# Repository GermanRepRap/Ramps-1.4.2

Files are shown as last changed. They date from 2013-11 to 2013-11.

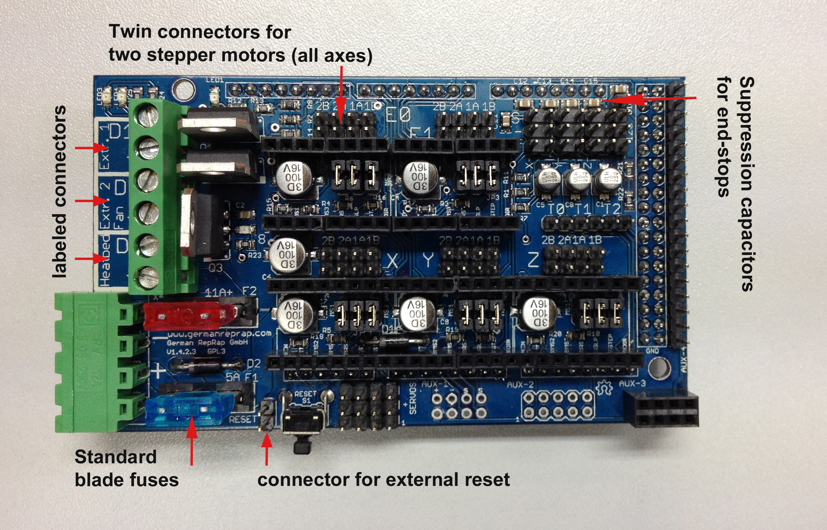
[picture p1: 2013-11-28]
Ramps142_1_beschriftet_EN.jpg

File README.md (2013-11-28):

Ramps-1.4.2
===========

forked from ultimachine/Ramps 1.4

The RAMPS 1.4.2 Change log

* Standard blade fuses instead of thermal fuses increasing the heat resilience.
 	
* Current carrying improved by increasing the thickness of the cooper at the PCB from 35 to 70 micro meters.

* Suppression caps added to each end-stop to avoid spurious signals.

* Added an additional connector to XY, E1 and E2 to connect a second stepper motor.

* Connector for external reset added.

* Labeled D8, D9,D10 with Heatbed, Extrude 1, Fan and Extruder 2.

Fully assembled available from German RepRap www.germanreprap.com

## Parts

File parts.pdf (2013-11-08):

StÃ¼ckliste exportiert aus /Users/markus/Documents/Arbeit/grrf/ ramps 1_42_3/RAMPS_1-42.3.sch am 17.07.13 03:23

Qty Value | Device | Package | Parts | Description | MF MPN OC_FARNELL OC_NEWARK
1 | 31-XX | B3F-31XX | S1 | OMRON SWITCH | B3F-
3100 959704 | 36M3582
10 | 3PIN-HEADER | 3PIN-HEADER

SER1,
SER2,
SER3,
SER4,
X+, X-,
Y+, Y-,
Z+, Z-

PIN HEADER

6 | C-EUC0805 | C0805 | C11, C12, C13, C14, C15, C16 | CAPACITOR, European symbol
2 | FUSE_MCCQ-122 | FUSE_MCCQ-122 | F1, F2
4 | LEDCHIP-LED0805 | CHIP-LED0805 | LED1, LED2, LED3, LED4 | LED
1 | M06SIP | 1X06 | JP7 | Header 6
13 | PINHD-1X4 | 1X04

A-OUT,
E0-
MOT,
E0-
MOT1,
E1-
MOT,
E1-
MOT1,
I2C,
SERIAL,
X-MOT,
X-MOT1,
Y-MOT,
Y-MOT1,
Z-MOT,
Z-MOT1

PIN HEADER

5 | PINHD-2X3 | 2X03

JP2, JP3,
JP4, JP5,
JP6

PIN HEADER

3 | 1.8K | R-US_R0805 | R0805

R23,
R24,
R25

RESISTOR,
American
symbol
8 | 100k | R-US_R0805 | R0805

R2, R3,
R4, R5,
R6, R8,
R9, R10

RESISTOR,
American
symbol
1 | 100nF | C-EUC0805 | C0805 | C2

CAPACITOR,
European
symbol
6 | 100uF | CPOL-US153CLV-0605 | 153CLV-0605 | C3, C4, C6, C7, C9, C10

POLARIZED
CAPACITOR,
American
symbol
5 | 10k | R-US_R0805 | R0805

R16,
R17,
R18,
R19,
R20

RESISTOR,
American
symbol
1 | 10r | R-US_M0805 | M0805 | R14 RESISTOR, American symbol
2 | 10r | R-US_R0805 | R0805 | R13, R15 RESISTOR, American symbol
3 | 10uF | CPOL-US153CLV-0405 | 153CLV-0405 | C1, C5, C8 POLARIZED CAPACITOR, American symbol
1 | 1K | R-US_R0805 | R0805 | R12 RESISTOR, American symbol
2 | 1N4004 | 1N4004 | DO41-10 | D1, D2 DIODE

1 | 282837-6 | 282837-6 | 282837-6 | U$2
5 | 4.7K | R-US_R0805 | R0805

R1, R7,
R11,
R21,
R22

RESISTOR,
American
symbol
5 | A4988BREAKOUT | A4988BREAKOUT | A4988BREAKOUT | U$4,
| | | | U$5,
| | | | U$6,
| | | | U$7,
| | | | U$8
1 | ARDUINO_MEGA_SHIELD ARDUINO_MEGA_SHIELD ARDUINO_MEGA_SHIELD U1
1 | M04X2 | M04X2 | 2X4 | U$3
1 | M05X2 | M05X2 | 2X5 | U$10
1 | M18_ | M18_ | 1X18 | U$9
1 | MSTBA4 | MSTBA4 | MSTBA4 | X4 | PHOENIX
1 | OSHW_LOGO_6MILX0100-
| NT | OSHW_LOGO_6MILX0100-
| | NT | OSHW_6X100_NOTEXT | LOGO1
1 | PINHD-2 | PINHD-2 | PINHD-2 | RESET
3 | STP55NF06L | IRF512 | TO220BV | Q1, Q2,
| | | | Q3 | N-CHANNEL
| | | | | MOS FET

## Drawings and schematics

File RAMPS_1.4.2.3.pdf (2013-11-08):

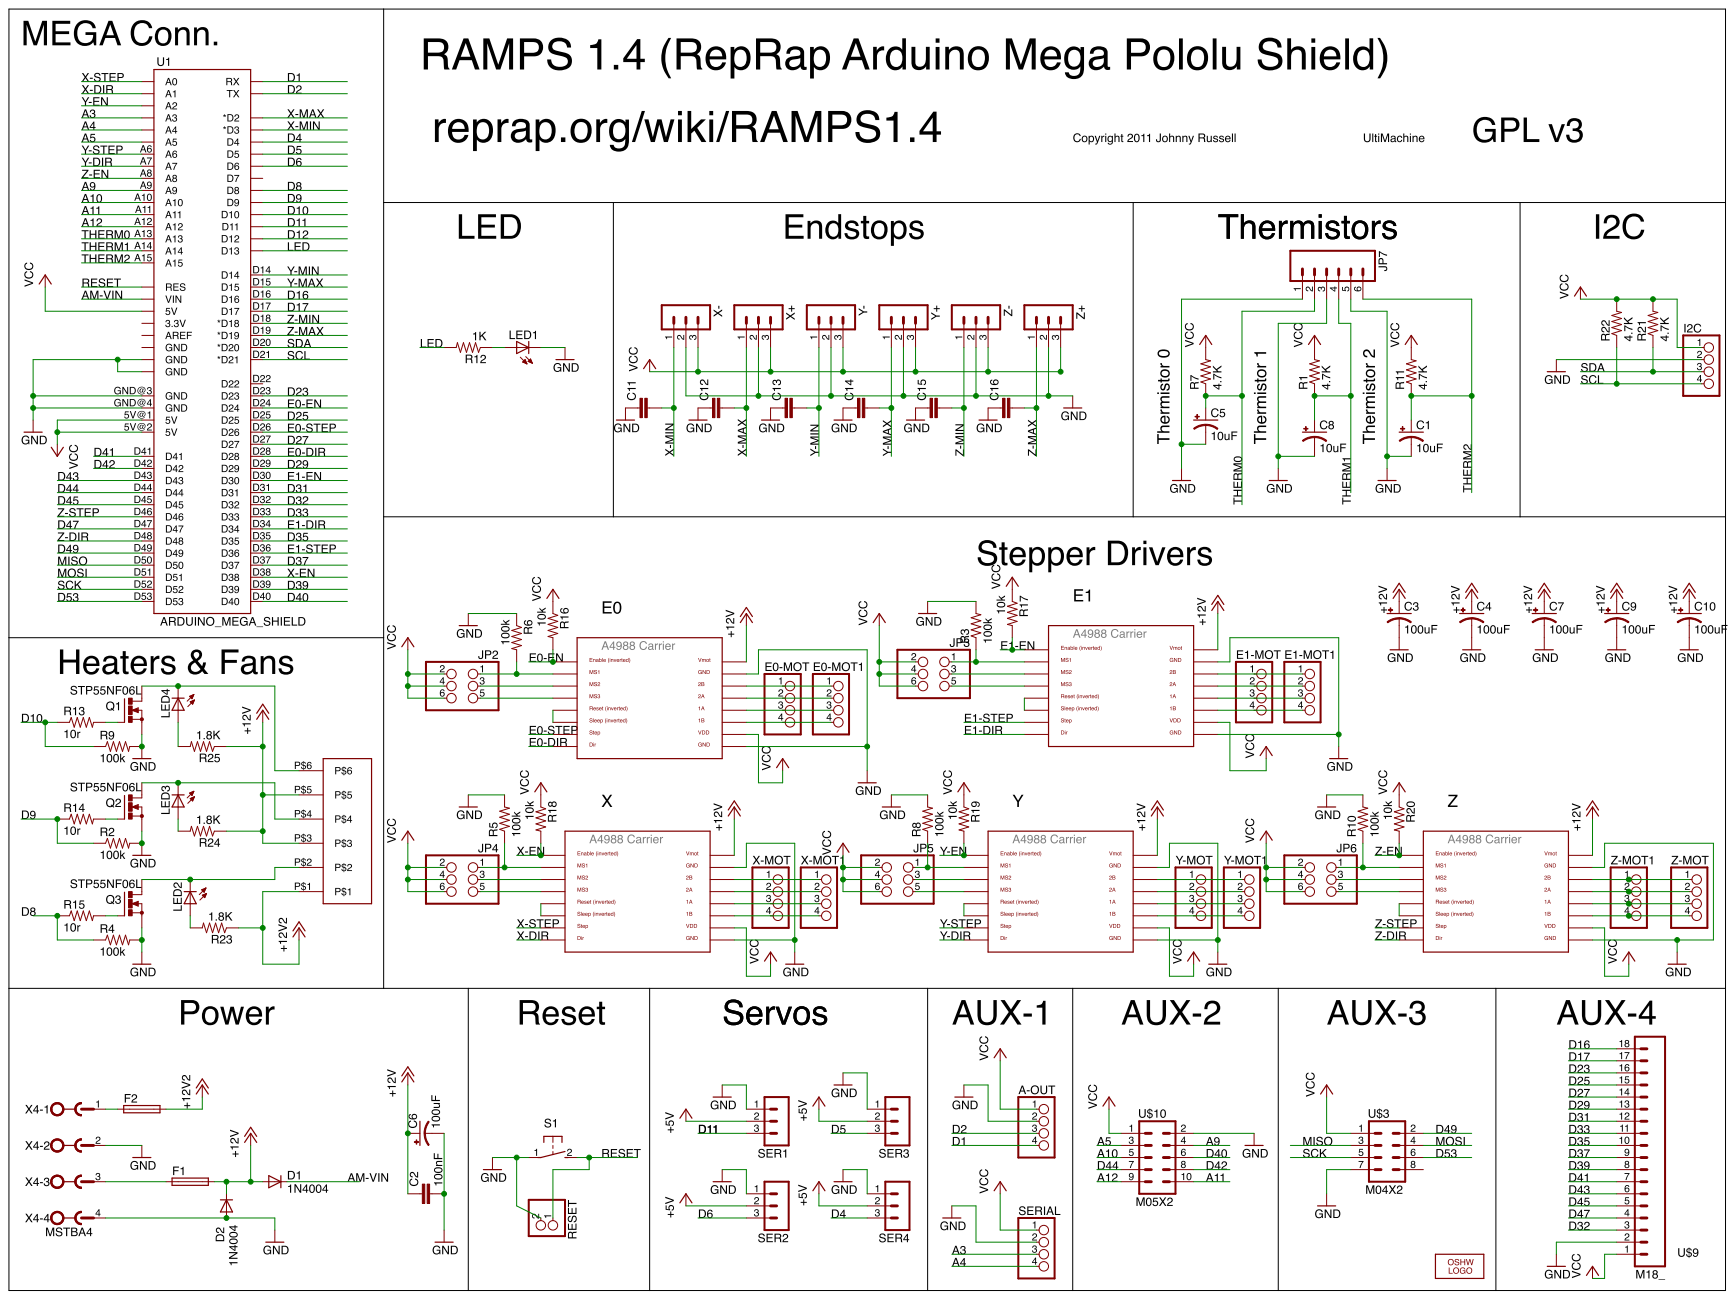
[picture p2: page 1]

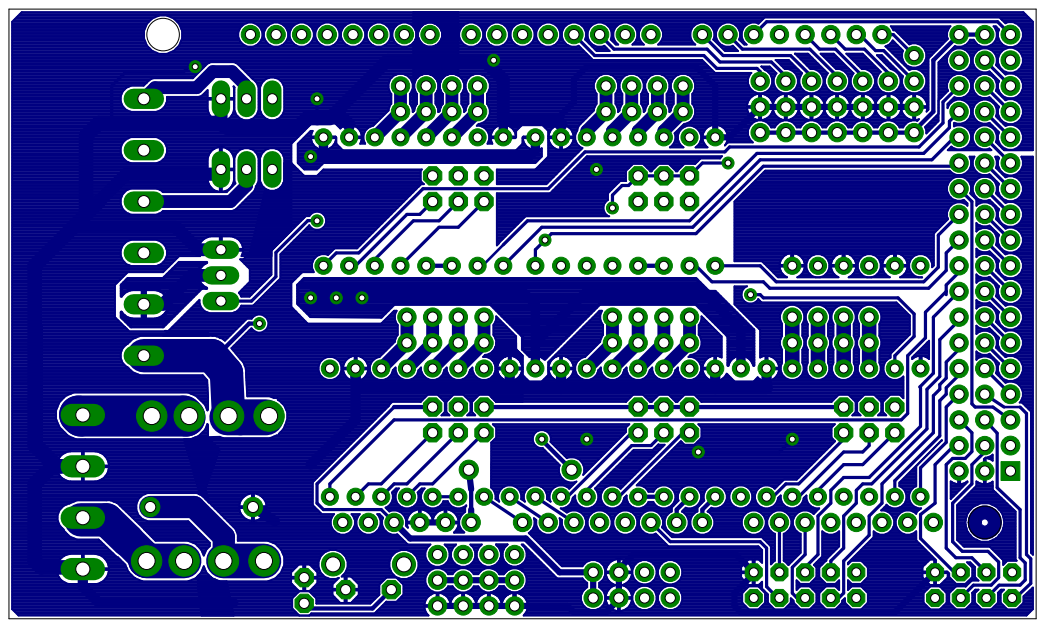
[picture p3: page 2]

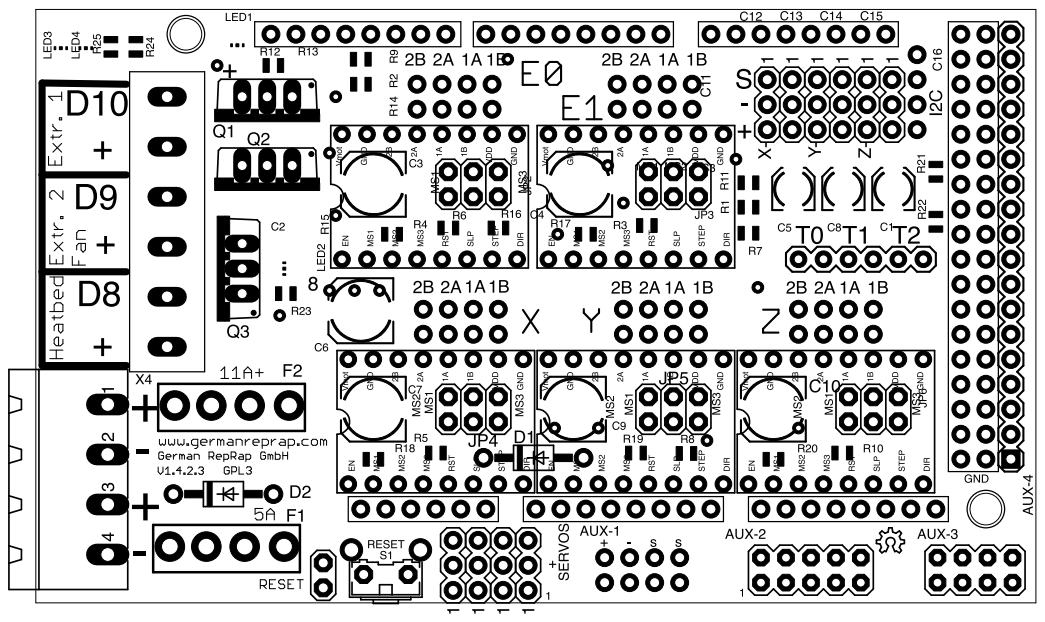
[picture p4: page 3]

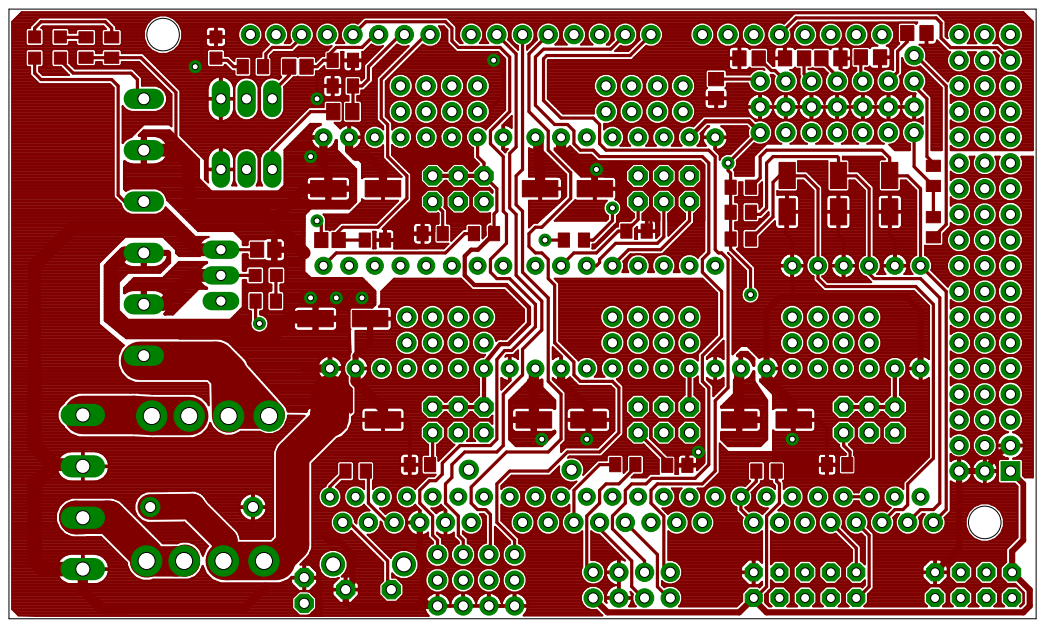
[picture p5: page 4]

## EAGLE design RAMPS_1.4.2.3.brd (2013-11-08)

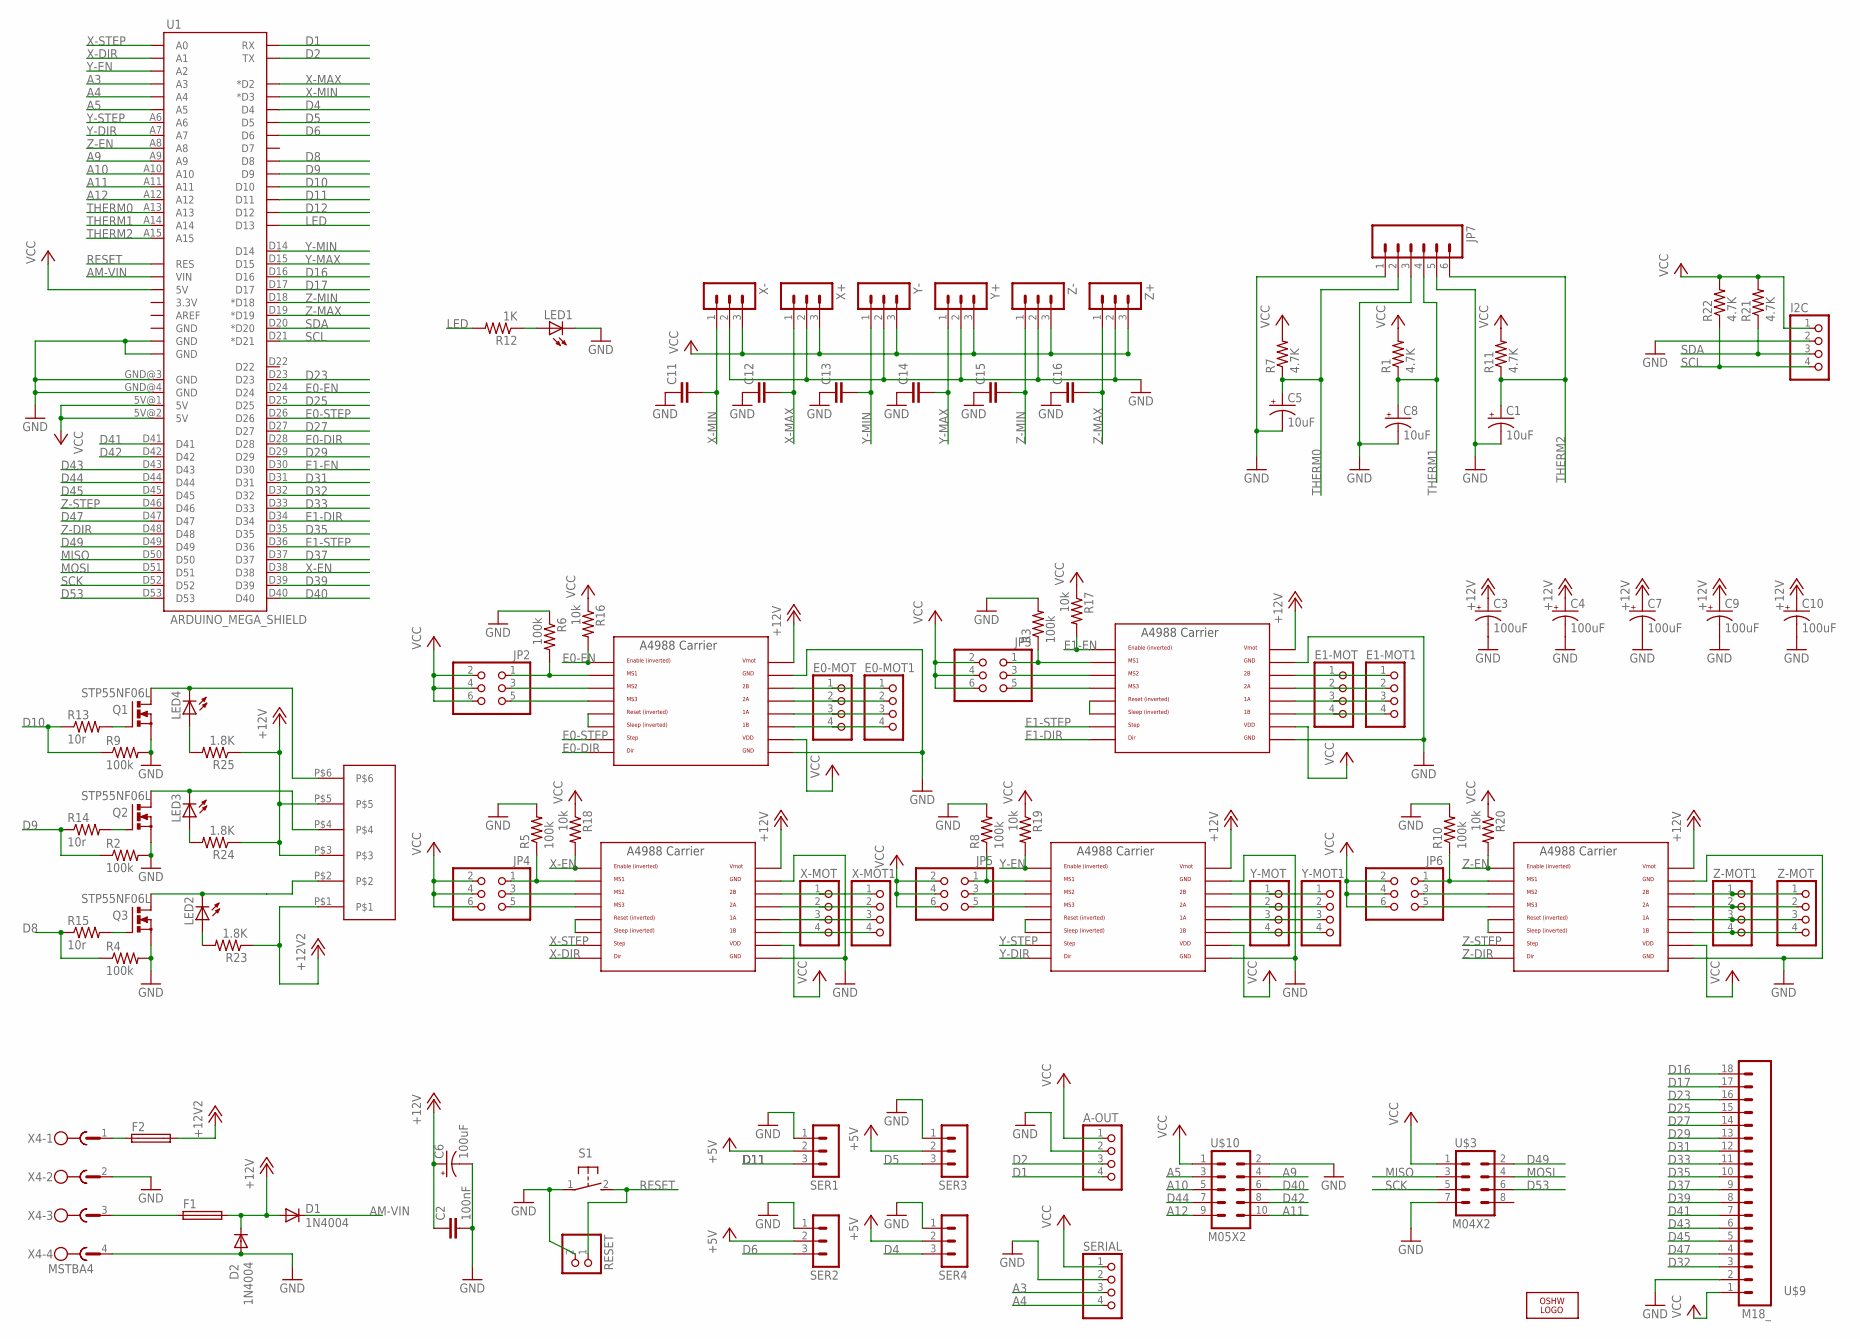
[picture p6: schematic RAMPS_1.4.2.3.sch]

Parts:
A-OUT: PINHD-1X4; 1X04
C1, C5, C8: 10uF; 153CLV-0405
C2: 100nF; C0805
C3, C4, C6, C7, C9, C10: 100uF; 153CLV-0605
C11, C12, C13, C14, C15, C16: C-EUC0805; C0805
D1, D2: 1N4004; DO41-10
E0-MOT, E0-MOT1, E1-MOT, E1-MOT1: PINHD-1X4; 1X04
F1, F2: FUSE_MCCQ-122
I2C: PINHD-1X4; 1X04
JP2, JP3, JP4, JP5, JP6: PINHD-2X3; 2X03
JP7: M06SIP; 1X06
LED1, LED2, LED3, LED4: LEDCHIP-LED0805; CHIP-LED0805
LOGO1: OSHW_LOGO_6MILX0100-NT; OSHW_6X100_NOTEXT
Q1, Q2, Q3: STP55NF06L; TO220BV
R1, R7, R11, R21, R22: 4.7K; R0805
R2, R3, R4, R5, R6, R8, R9, R10: 100k; R0805
R12: 1K; R0805
R13, R15: 10r; R0805
R14: 10r; M0805
R16, R17, R18, R19, R20: 10k; R0805
R23, R24, R25: 1.8K; R0805
RESET: PINHD-2
S1: 31-XX; B3F-31XX
SER1, SER2, SER3, SER4: 3PIN-HEADER
SERIAL: PINHD-1X4; 1X04
U1: ARDUINO_MEGA_SHIELD
U$2: 282837-6
U$3: M04X2; 2X4
U$4, U$5, U$6, U$7, U$8: A4988BREAKOUT
U$9: M18_; 1X18
U$10: M05X2; 2X5
X4: MSTBA4
X+: 3PIN-HEADER
X-: 3PIN-HEADER
X-MOT, X-MOT1: PINHD-1X4; 1X04
Y+: 3PIN-HEADER
Y-: 3PIN-HEADER
Y-MOT, Y-MOT1: PINHD-1X4; 1X04
Z+: 3PIN-HEADER
Z-: 3PIN-HEADER
Z-MOT, Z-MOT1: PINHD-1X4; 1X04

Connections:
+5V: SER1.2, SER2.2, SER3.2, SER4.2
+12V: C2.1, C3.+, C4.+, C6.+, C7.+, C9.+, C10.+, D1.A, D2.C, F1.2-1 (2), F1.2-2 (2), R24.1, R25.1, U$2.P$3, U$2.P$5, U$4.VMOT, U$5.VMOT, U$6.VMOT, U$7.VMOT, U$8.VMOT
+12V2: F2.2-1 (2), F2.2-2 (2), R23.1, U$2.P$1
A3: SERIAL.3, U1.A3
A4: SERIAL.4, U1.A4
A5: U1.A5, U$10.3
A9: U1.A9, U$10.4
A10: U1.A10, U$10.5
A11: U1.A11, U$10.10
A12: U1.A12, U$10.9
AM-VIN: D1.C, U1.VIN
D1: A-OUT.4, U1.RX
D2: A-OUT.3, U1.TX
D4: SER4.3, U1.D4
D5: SER3.3, U1.D5
D6: SER2.3, U1.D6
D8: R4.1, R15.1, U1.D8
D9: R2.1, R14.1, U1.D9
D10: R9.1, R13.1, U1.D10
D11: SER1.3, U1.D11
D12: U1.D12
D16: U1.D16, U$9.18
D17: U1.D17, U$9.17
D23: U1.D23, U$9.16
D25: U1.D25, U$9.15
D27: U1.D27, U$9.14
D29: U1.D29, U$9.13
D31: U1.D31, U$9.12
D32: U1.D32, U$9.3
D33: U1.D33, U$9.11
D35: U1.D35, U$9.10
D37: U1.D37, U$9.9
D39: U1.D39, U$9.8
D40: U1.D40, U$10.6
D41: U1.D41, U$9.7
D42: U1.D42, U$10.8
D43: U1.D43, U$9.6
D44: U1.D44, U$10.7
D45: U1.D45, U$9.5
D47: U1.D47, U$9.4
D49: U1.D49, U$3.2
D53: U1.D53, U$3.6
E0-DIR: U1.D28, U$4.DIR
E0-EN: R16.2, U1.D24, U$4.EN
E0-STEP: U1.D26, U$4.STEP
E1-DIR: U1.D34, U$5.DIR
E1-EN: R17.2, U1.D30, U$5.EN
E1-STEP: U1.D36, U$5.STEP
GND: A-OUT.2, C1.-, C2.2, C3.-, C4.-, C5.-, C6.-, C7.-, C8.-, C9.-, C10.-, C11.1, C12.1, C13.1, C14.1, C15.1, C16.1, D2.A, I2C.2, JP7.1, JP7.3, JP7.5, LED1.C, Q1.S, Q2.S, Q3.S, R2.2, R3.2, R4.2, R5.2, R6.1, R8.2, R9.2, R10.2, RESET.2, S1.1, SER1.1, SER2.1, SER3.1, SER4.1, SERIAL.2, U1.GND@0 (GND), U1.GND@1 (GND), U1.GND@3 (GND), U1.GND@4 (GND), U$3.7, U$4.GND, U$4.GND@0 (GND), U$5.GND, U$5.GND@0 (GND), U$6.GND, U$6.GND@0 (GND), U$7.GND, U$7.GND@0 (GND), U$8.GND, U$8.GND@0 (GND), U$9.2, U$10.2, X4.2, X4.4, X+.2, X-.2, Y+.2, Y-.2, Z+.2, Z-.2
LED: R12.2, U1.D13
MISO: U1.D50, U$3.3
MOSI: U1.D51, U$3.4
unnamed: LED3.C, Q2.D, U$2.P$4
unnamed: E0-MOT.1, E0-MOT1.1, U$4.2B
unnamed: E0-MOT.2, E0-MOT1.2, U$4.2A
unnamed: JP2.1, R6.2, U$4.MS1
unnamed: JP2.5, U$4.MS3
unnamed: LED4.C, Q1.D, U$2.P$6
unnamed: U$4.RST, U$4.SLP (SLEEP)
unnamed: JP2.3, U$4.MS2
unnamed: E0-MOT.3, E0-MOT1.3, U$4.1A
unnamed: E0-MOT.4, E0-MOT1.4, U$4.1B
unnamed: E1-MOT.1, E1-MOT1.1, U$5.2B
unnamed: E1-MOT.2, E1-MOT1.2, U$5.2A
unnamed: JP4.1, R5.1, U$6.MS1
unnamed: JP4.3, U$6.MS2
unnamed: E1-MOT.3, E1-MOT1.3, U$5.1A
unnamed: JP5.3, U$7.MS2
unnamed: E1-MOT.4, E1-MOT1.4, U$5.1B
unnamed: JP4.5, U$6.MS3
unnamed: U$6.RST, U$6.SLP (SLEEP)
unnamed: U$6.2B, X-MOT.1, X-MOT1.1
unnamed: U$6.2A, X-MOT.2, X-MOT1.2
unnamed: U$7.RST, U$7.SLP (SLEEP)
unnamed: U$5.RST, U$5.SLP (SLEEP)
unnamed: JP3.1, R3.1, U$5.MS1
unnamed: U$6.1A, X-MOT.3, X-MOT1.3
unnamed: U$6.1B, X-MOT.4, X-MOT1.4
unnamed: U$7.2B, Y-MOT.1, Y-MOT1.1
unnamed: U$7.2A, Y-MOT.2, Y-MOT1.2
unnamed: U$7.1A, Y-MOT.3, Y-MOT1.3
unnamed: JP5.5, U$7.MS3
unnamed: LED2.A, R23.2
unnamed: JP5.1, R8.1, U$7.MS1
unnamed: JP3.5, U$5.MS3
unnamed: JP3.3, U$5.MS2
unnamed: U$7.1B, Y-MOT.4, Y-MOT1.4
unnamed: JP6.3, U$8.MS2
unnamed: U$8.RST, U$8.SLP (SLEEP)
unnamed: JP6.5, U$8.MS3
unnamed: JP6.1, R10.1, U$8.MS1
unnamed: U$8.2B, Z-MOT.1, Z-MOT1.1
unnamed: U$8.2A, Z-MOT.2, Z-MOT1.2
unnamed: U$8.1A, Z-MOT.3, Z-MOT1.3
unnamed: U$8.1B, Z-MOT.4, Z-MOT1.4
unnamed: LED3.A, R24.2
unnamed: LED1.A, R12.1
unnamed: Q2.G, R14.2
unnamed: Q1.G, R13.2
unnamed: Q3.G, R15.2
unnamed: LED4.A, R25.2
unnamed: LED2.C, Q3.D, U$2.P$2
unnamed: F2.1-1 (1), F2.1-2 (1), X4.1
unnamed: F1.1-1 (1), F1.1-2 (1), X4.3
RESET: RESET.1, S1.2 (S), U1.RES
SCK: U1.D52, U$3.5
SCL: I2C.4, R22.1, U1.D21 (*D21)
SDA: I2C.3, R21.1, U1.D20 (*D20)
THERM0: C5.+, JP7.2, R7.1, U1.A13
THERM1: C8.+, JP7.4, R1.1, U1.A14
THERM2: C1.+, JP7.6, R11.1, U1.A15
VCC: A-OUT.1, I2C.1, JP2.2, JP2.4, JP2.6, JP3.2, JP3.4, JP3.6, JP4.2, JP4.4, JP4.6, JP5.2, JP5.4, JP5.6, JP6.2, JP6.4, JP6.6, R1.2, R7.2, R11.2, R16.1, R17.1, R18.1, R19.1, R20.1, R21.2, R22.2, SERIAL.1, U1.5V@0 (5V), U1.5V@1 (5V), U1.5V@2 (5V), U$3.1, U$4.VDD, U$5.VDD, U$6.VDD, U$7.VDD, U$8.VDD, U$9.1, U$10.1, X+.3, X-.3, Y+.3, Y-.3, Z+.3, Z-.3
X-DIR: U1.A1, U$6.DIR
X-EN: R18.2, U1.D38, U$6.EN
X-MAX: C12.2, U1.D2 (*D2), X+.1
X-MIN: C11.2, U1.D3 (*D3), X-.1
X-STEP: U1.A0, U$6.STEP
Y-DIR: U1.A7, U$7.DIR
Y-EN: R19.2, U1.A2, U$7.EN
Y-MAX: C14.2, U1.D15, Y+.1
Y-MIN: C13.2, U1.D14, Y-.1
Y-STEP: U1.A6, U$7.STEP
Z-DIR: U1.D48, U$8.DIR
Z-EN: R20.2, U1.A8, U$8.EN
Z-MAX: C16.2, U1.D19 (*D19), Z+.1
Z-MIN: C15.2, U1.D18 (*D18), Z-.1
Z-STEP: U1.D46, U$8.STEP

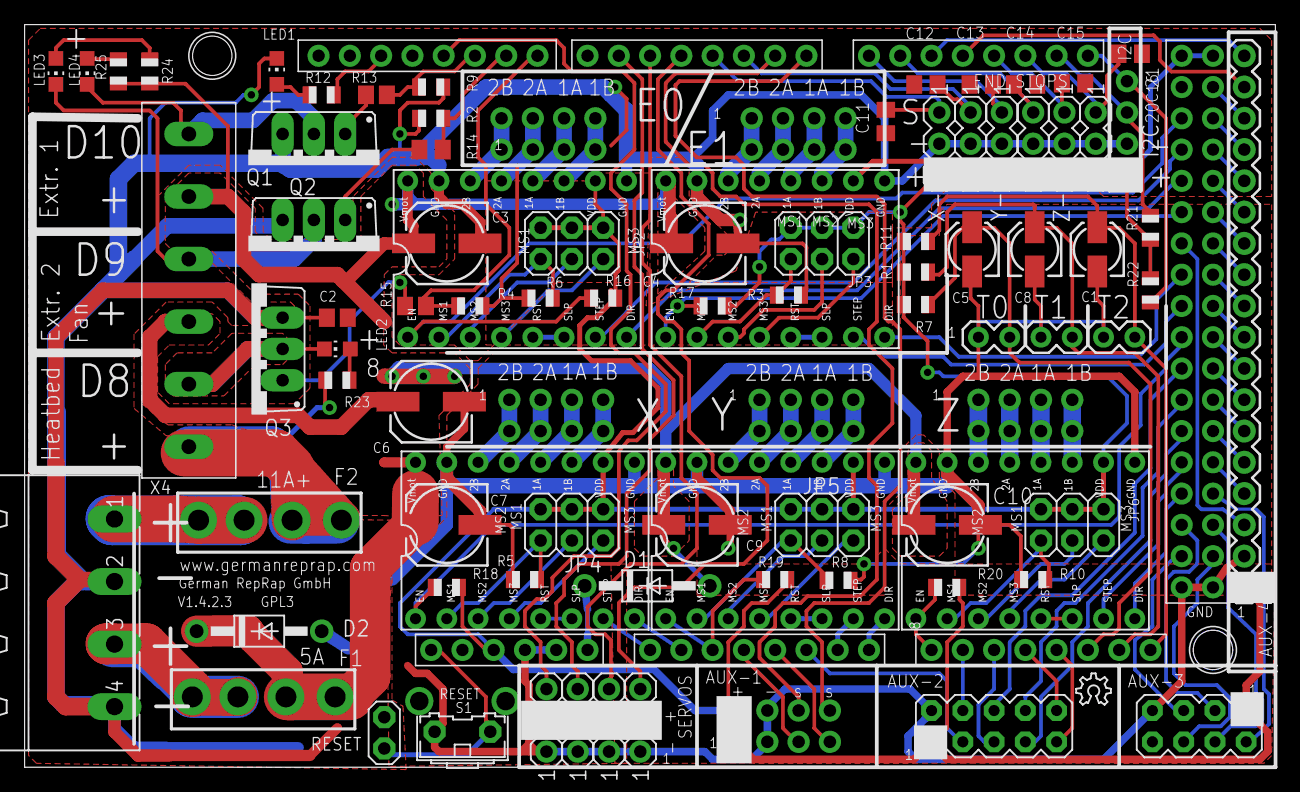
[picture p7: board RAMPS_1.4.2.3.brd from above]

Board: 2 copper layers, 101.6 x 60.3 mm, 95 parts (0 on the bottom side), 126 nets.

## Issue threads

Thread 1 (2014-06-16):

nicht für 24v Betrieb sutable

ellensp, 2014-06-16:
Coverted mit Google Translate, so aplogies für schlechtes Deutsch.

Wenn Sie die Pololu Kondensatoren 35volt aktualisieren, würde Ihre Bord bereit 24Volt werden.
So dass es noch besser :)

Auch, warum hast du das nicht auf die reprap Wiki hinzufügen?

burdickjp, 2016-05-14:
I would also appreciate capacitors to allow 24V. I am having to replace mine and it's difficult to solder down in between the tall headers.

Closed 2020-04-26.

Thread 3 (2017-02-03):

missing capacitor values in part list for the endstops

3DSTB, 2017-02-03:
What is the right value for the capacitors C11, C12, C13, C14, C15 and C16? These capacitors are for the endstops and not on the regular ramps. I think it is the same value as on C2 (100 nF).

Please clarify.

behnam68, 2017-10-12:
Hello
I have the same question.May i know the value of capacitors C11-16?
Best regards

behnam68, 2017-10-31:
Hi dear @3DSTB
Can you find the correct answer?

corbolais, 2019-06-13:
@behnam68 @3DSTB start using 10nF for endstop debouncing (filterin).

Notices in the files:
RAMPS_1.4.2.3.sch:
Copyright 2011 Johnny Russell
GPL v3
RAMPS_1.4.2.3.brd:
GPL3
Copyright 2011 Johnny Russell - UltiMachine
